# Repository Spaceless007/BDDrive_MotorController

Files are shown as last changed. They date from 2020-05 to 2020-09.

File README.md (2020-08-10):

# BDDrive_MotorController
Modifications done on the open source ODrive project to support one low current brushless DC motor

## Introduction
This project is based on a open source porjet named [ODrive](https://odriverobotics.com/). ODrive is a high power brushless DC motor controller. The main goal of the BDDrive is to modify the ODrive v3.4 to accomodate special needs for a tension controlled braided carrier of composites master's project. In short, there are two main reasons why the BDDrive was conceive. 

Firstly, the most recent ODrive someone can buy is the version v3.6, which was the board used first for testing if this board could be useful for the carrier. Almost everything about the ODrive is open source. The firmware is totally available for free [at this repository](https://github.com/madcowswe/ODrive). Most of the hardware is available, except for the most recent versions v3.5 and v3.6. The creator of the project started to see people copying the project and selling it at a lower price, so he decided to stop to make available the hardware design of the newer versions.Since the most recent board which is on the [hardware github repository](https://github.com/madcowswe/ODriveHardware) is the ODrive v3.4, and this board has many issues, well, it needed to be modified on the BDDrive.

Secondly, ODrive is a **high power** motor controller, it can control motors up to high current (something like 60 Amps, maybe even more). But the carrier is not using high power motors, the highest it goes is around 5 Amps. Since the ODrive is designed for higher current motors, it isn't the best for controlling motor like the tension controlled braided carrier is using. So we needed to fix this on the BDDrive. 

## Repository layout
Here is how the repository is organized and what folder contains what:
- Documentation: contains general documentation for the board
  - Ressources: contains various useful diagrams
  - Requirements: contains files where the requierements of the board are explained, what was modified and for what reason
  - Shunt test: contains screen shots of a test done using a ODrive v3.6 with new shunt resistors designed for low power DC brushless motors
- Hardware: contains the Altium Designer files for the BDDrive embedded circuit (electrical schematics)
  - CAD: contains .step files for electrical integrated circuits (IC) and also a .step file for the whole BDDrive board
  - BOM: contains the bill of materials for the board
  - gerbers: contains files generated with Altium Designer to produce the circuit with the JLC PCB or PCB Way company
  - Altium_libs: contains custom libraries for various electrical parts in the PCB (printed circuit board)
  - v3.4_nbd: contains the schematics and the PCB files for the BDDrive
  - v3: contains the schematics for the ODrive v3.4 board

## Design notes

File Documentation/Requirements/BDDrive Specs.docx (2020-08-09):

1. HARDWARE COMPARAISON

ODrive v3.4

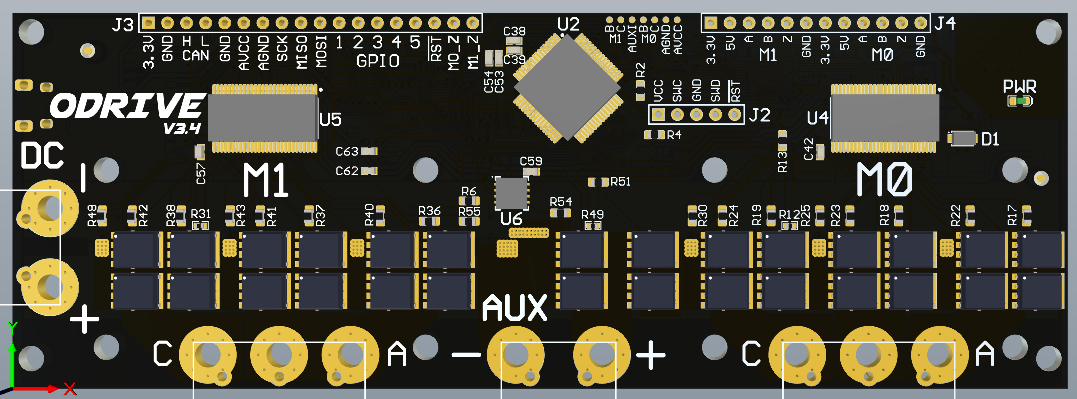
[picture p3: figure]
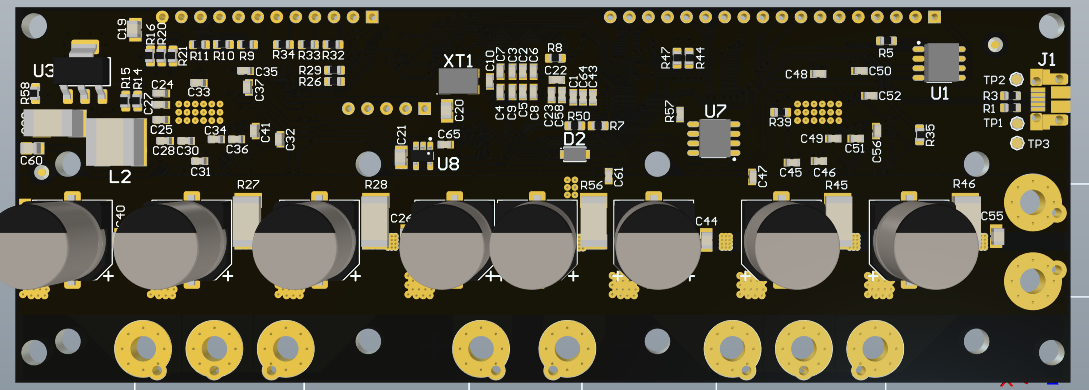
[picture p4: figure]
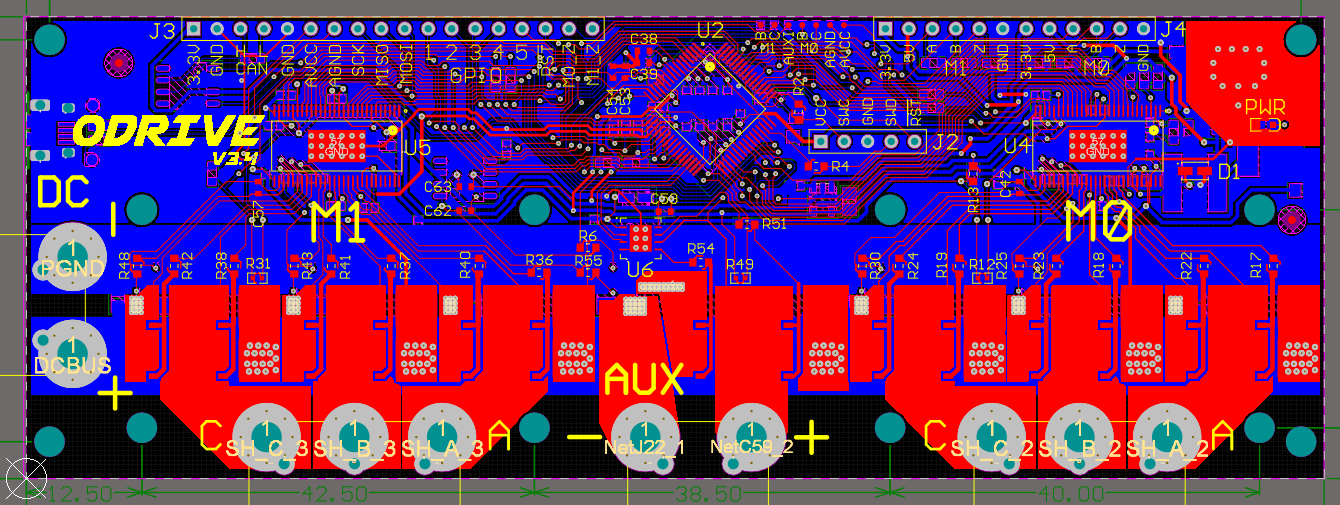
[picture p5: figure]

BDDrive : ODrive v3.4 modified

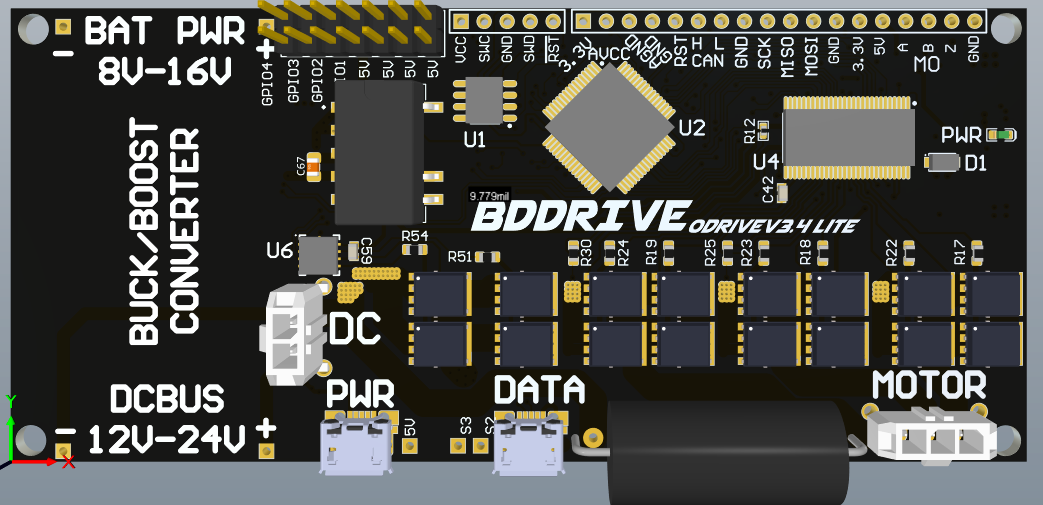
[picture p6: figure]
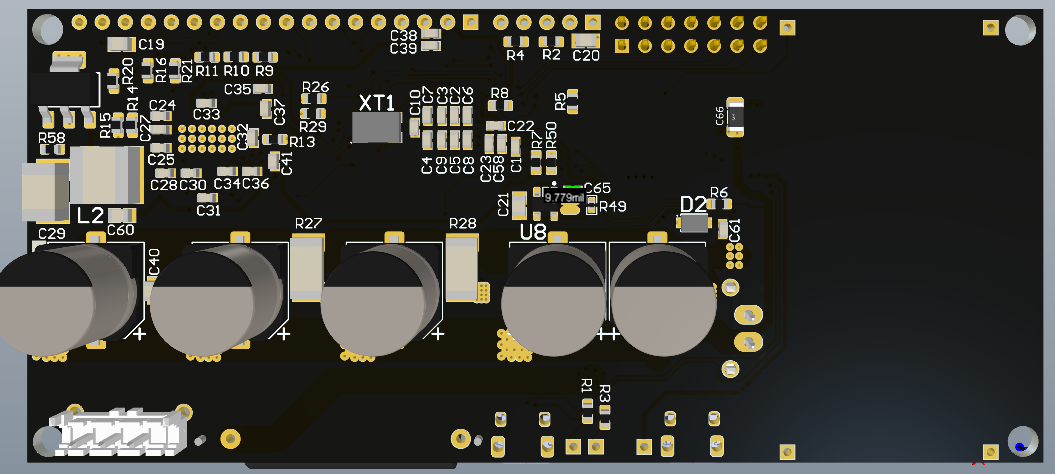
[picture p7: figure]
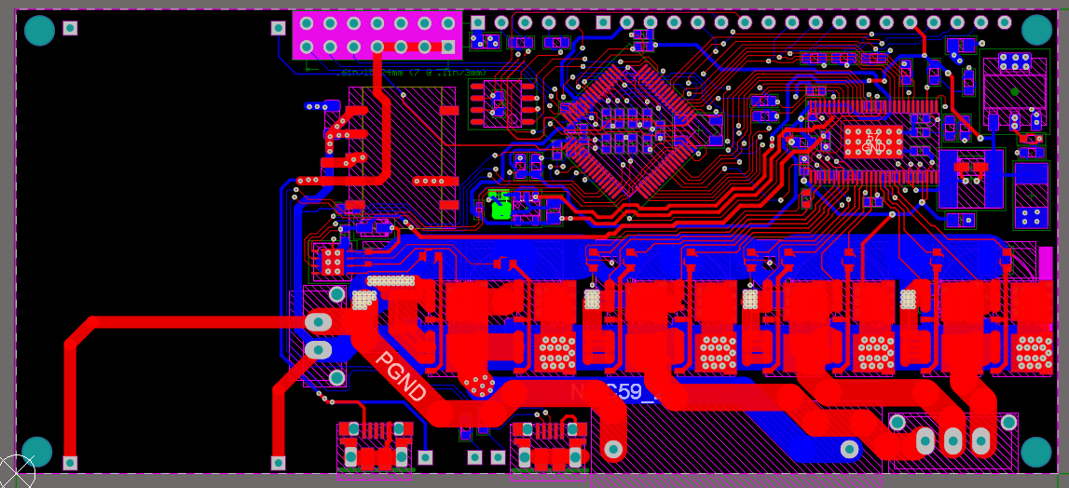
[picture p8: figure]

The polygon pours are not shown on this board, or else we wouldn`t see anything

2. MODIFICATIONS
- Remove support for two motors (remove M1), so right now BDDrive can only control one brushless DC motor
- Add support for a Buck/Boost converter breakout board soldered directly on the BDDrive
  - The breakout board needs to be within these specs: input from 8 to 16 volts and output configured as 12 to 24 volts
  - Don’t go over 24V (not even 24,5V), the BDDrive doesn’t support it
- Replace power resistor connector for a power resistor soldered directly on the board
  - Also, this resistor is rectangular (even though it is showed as round in the picture above) to be able to put mini heat sinks on it
- Use Molex connectors instead of screw in connectors to facilitate harness setup and the screw in connectors were proven as unreliable
- Add another 5V @ 1A power supply designed to power a Raspberry Pi with it (the power consumption of a Raspberry Pi Zero was estimated that the would be to be under 200 mA, so you can add 5V mini cooling fans with the 4 power pints available)
- Add external header with 5V supply outputs (4 power pins and 4 GND pins) and access to GPIO ports (3 GPIO pins and 3 GND pins)
- Add a power micro USB connector connected to the new 5V supply to power the Raspberry Pi
- Reroute a lot of components to minimize the size of the PCB
- Fix problems with the ODrive v3.4 which are documented here:
  - From the hardware GitHub: https://github.com/madcowswe/ODriveHardware
    - Check docs of v3.4 and v3.5 folders
    - Check CHANGELOG.md of v3 folder
  - https://discourse.odriverobotics.com/t/drv-fault-on-odrive-v3-4/558?u=madcowswe
  - Go from two layers to four layers to keep the GND uniformed
  - Fix routing problems
- Modify shunt resistors to be able to have a low power motor (below 5 Amps)
  - https://discourse.odriverobotics.com/t/current-sensing-resistor-for-low-current-motors/377/2
  - https://discourse.odriverobotics.com/t/maxon-272763-motor/989/8

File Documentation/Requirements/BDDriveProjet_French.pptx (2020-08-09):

## CONCEPTION D’UN CIRCUIT IMPRIMÉ POUR UN DÉBOBINEUR ASSERVI A FIL ROBOTISÉ POUR LE TRESSAGE NON-LINÉAIRE DES FIBRES COMPOSITES

NATHANAËL BEAUDOIN-DION
2020/05/07

## AGENDA

- Characterisation of single yarn microstructure

- Présentation du projet & des requis
- Ce qu’il a été fait
- Ce qu’il reste à faire
- Échéancier
- Budget

## PRÉSENTATION DU PROJET & DES REQUIS

NATHANAËL BEAUDOIN-DION
2020/05/07

## PRÉSENTATION DU PROJET

- Originalement, Cristian utilisait un circuit imprimé nommé ODrive v3.6 et il fonctionne bien
- Cependant, le PCB (Printed Circuit Board) est trop gros et il supporte deux moteurs, ce qui n’est pas necessaire
- Ainsi, je suis parti du schema électrique du ODrive v3.4 (v3.6 n’est pas disponible) pour ensuite le modifier
- Donc ce PCB doit controller un moteur et il doit communiquer avec un Raspberry Pi afin de pouvoir être controlé à distance (projet de Mathieu)

## PRÉSENTATION DU PROJET

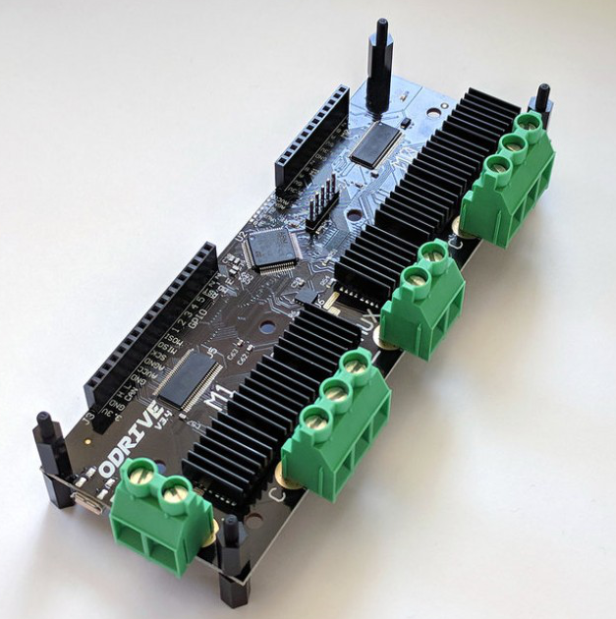
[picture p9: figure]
ODrive v3.6 24V on RoboRium in India Canada USA Bangladesh Nepal ...

ODrive v3.6

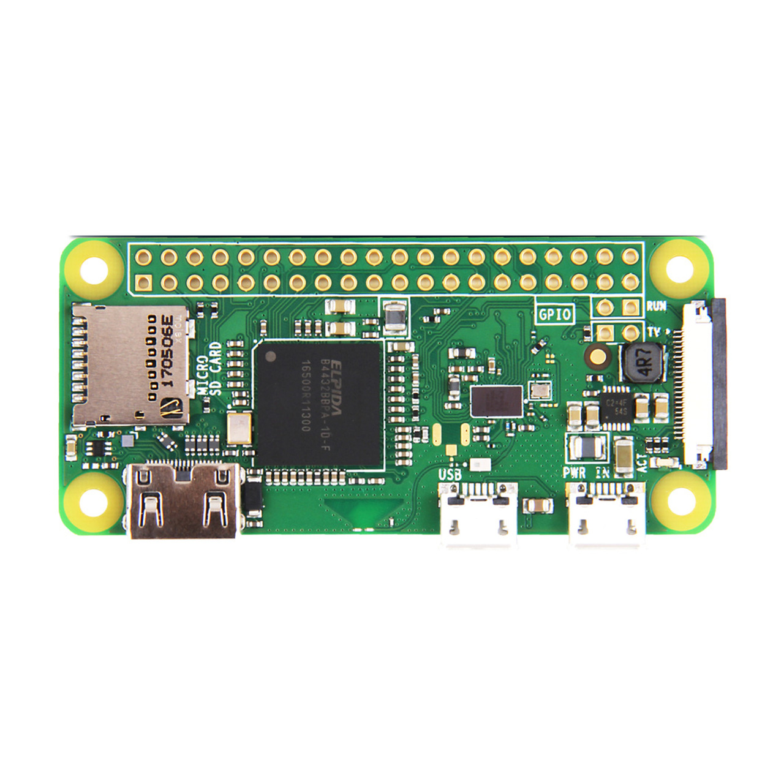
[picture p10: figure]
Raspberry Pi Zero W

Raspberry Pi Zero W

## PRÉSENTATION DES REQUIS

Le ODrive modifié, appelé BDDrive, doit :
- Contrôler un moteur de type “brushless” à l’aide d’un encodeur précisément
- Freiner le moteur avec une résistance de puissance intégrée au PCB
- Communiquer en sériel avec un connecteur microUSB
- Être alimenté par une batterie par différents voltages (12v, 15v, 20v, 24v) puis calibrer son alimentation à 12V
- Alimenté avec du 5V le Raspberry Pi avec un connecteur microUSB
- Avoir des pins “varia” pour par exemple alimenté des ventilateurs
- Être le plus petit possible

## CE QU’IL A ÉTÉ FAIT

NATHANAËL BEAUDOIN-DION
2020/05/07

## CE QU’IL A ÉTÉ FAIT

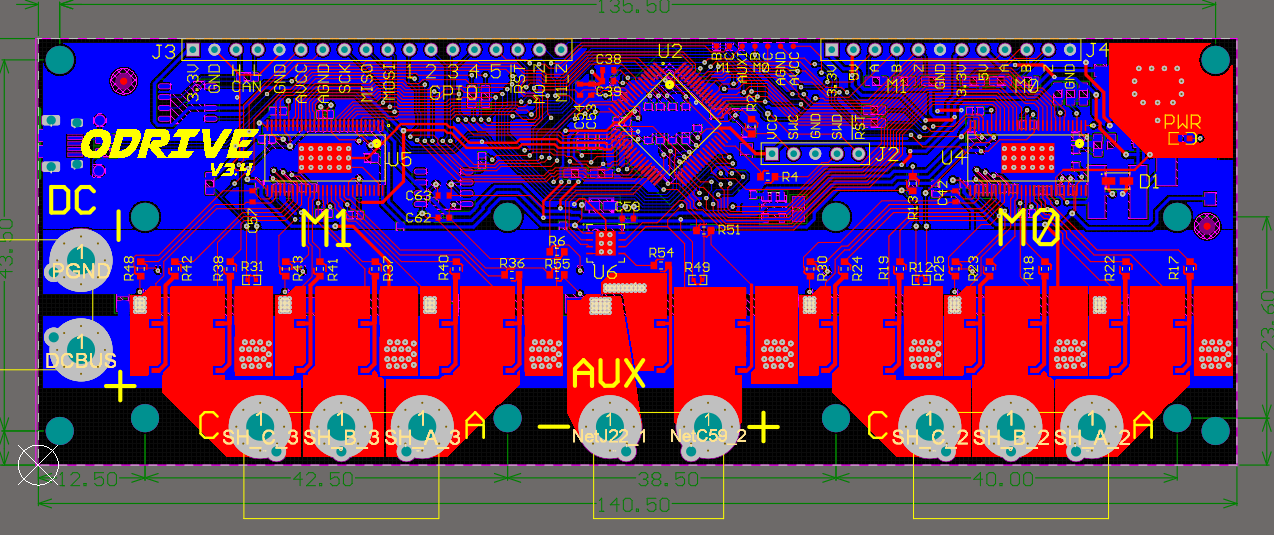
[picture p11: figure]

BDDrive

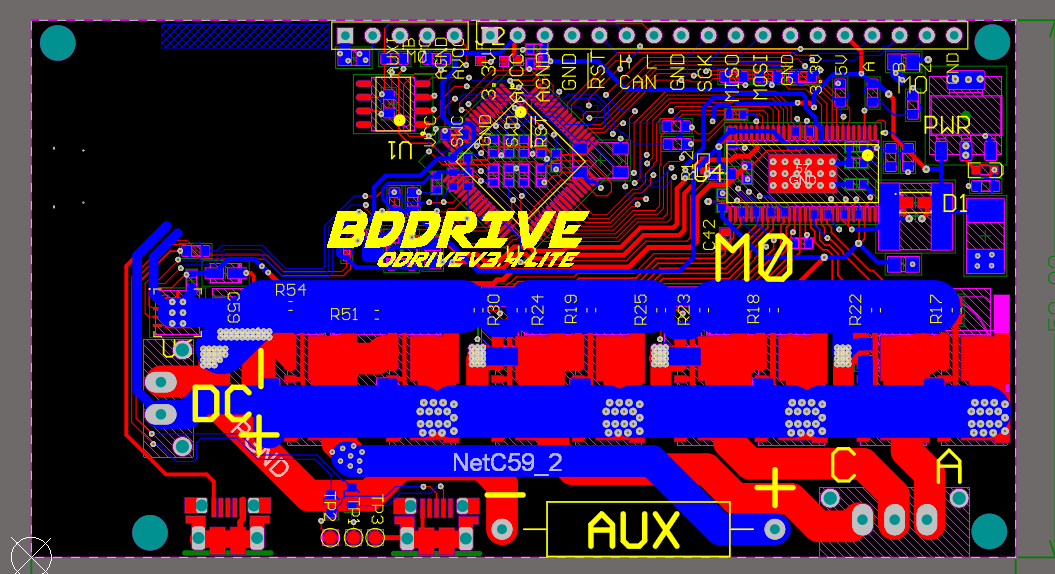
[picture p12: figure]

ODrive v3.4

## CE QU’IL A ÉTÉ FAIT

- Plusieurs tests sur le ODrive v3.6 et ODrive v3.4 ont été fait afin de vérifier leur fonctionnement
  - Pour v3.6 : changer des résistances pour diminuer le bruit
  - Pour v3.4 : vérifier qu’il fonctionne normalement
- Design à partir du ODrive v3.4 le BDDrive
  - Régler plusieurs problèmes présents dans le PCB au niveau logique et physique
  - Reroutage du PCB afin de diminuer sa taille le plus possible
  - Ajouter des nouvelles résistances
  - Modification des connecteurs (pour diminuer la taille du PCB)
  - Ajout d’un connecteur microUSB pour alimenté le Raspberry Pi

## CE QU’IL A ÉTÉ FAIT

- Recherche et compréhension générale du projet Open Source ODrive, comment le faire fonctionner, debug les problèmes du setup de programmation
  - 10h00
- Tests avec le ODrive 3.6 avec deux tests benchs différents (pré et post COVID)
  - 8h00
- Production et soudure du ODrive v3.4
  - 14h00
- Premiers tests sur le ODrive v3.4
  - 4h00
- Début du design du BDDrive, recherche sur internet de ses problèmes
  - 26h00

## CE QU’IL RESTE À FAIRE

NATHANAËL BEAUDOIN-DION
2020/05/07

## CE QU’IL RESTE À FAIRE

- Finir les tests sur ODrive v3.4 (5h00)
  - Tests software
- Finir le design du BDDrive (20h00)
  - Ajout du régulateur de tensión 5V 1A pour l’alimentation du Raspberry Pi
  - Ajout du circuit d’alimentation du BDDrive à partir d’une batterie, avec différents voltages afin de output un 12V constant
  - Ajout d’un connecteur varia
  - Ajout d’une lecture de tension de la batterie
- Production et soudure du BDDrive (12h00 de travail, mais beaucoup d’attente)
  - Peut potentiellement prendre beaucoup de temps à cause du COVID-19
- Tests du BDDrive (minimum 5h)

## ÉCHÉANCIER

NATHANAËL BEAUDOIN-DION
2020/05/07

## ÉCHÉANCIER DU MOIS DE MAI

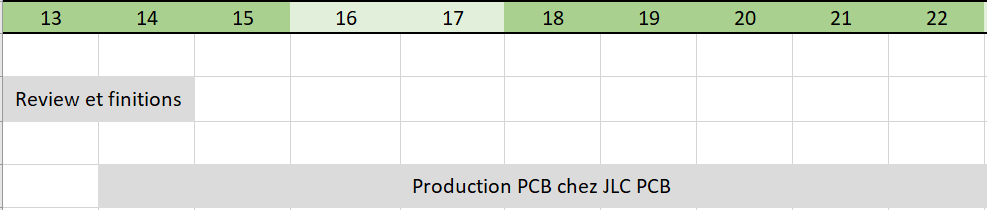
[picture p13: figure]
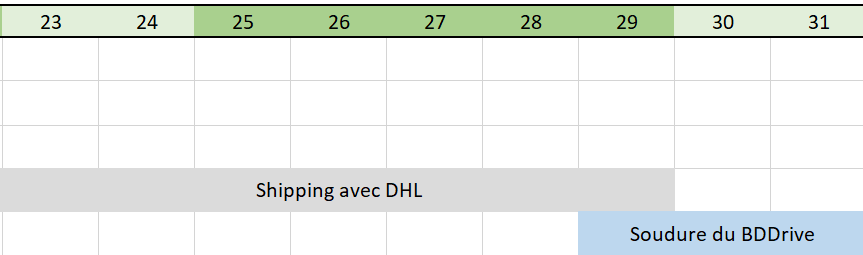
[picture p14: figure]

## BUDGET

NATHANAËL BEAUDOIN-DION
2020/05/07

## BUDGET

- Ce qu’il a déjà été dépensé :
  - Production et soudure du ODrive v3.4 : 229.25 CAD $ + 30.10 USD $
- Ce qu’il reste à dépensé pour la conception du BDDrive :
  - Production PCB à 5 exemplaires en 5 jours: 75 USD $ (+29 en 3 jours, +58 en 2 jours)
  - Production PCB à 100 exemplaires en 8 jours: 215 USD $
  - Pièces électroniques pour 1 exemplaire : environ 100 CAD $
  - Pièces électroniques pour 100 exemplaires : au dessus de 6,000 CAD $

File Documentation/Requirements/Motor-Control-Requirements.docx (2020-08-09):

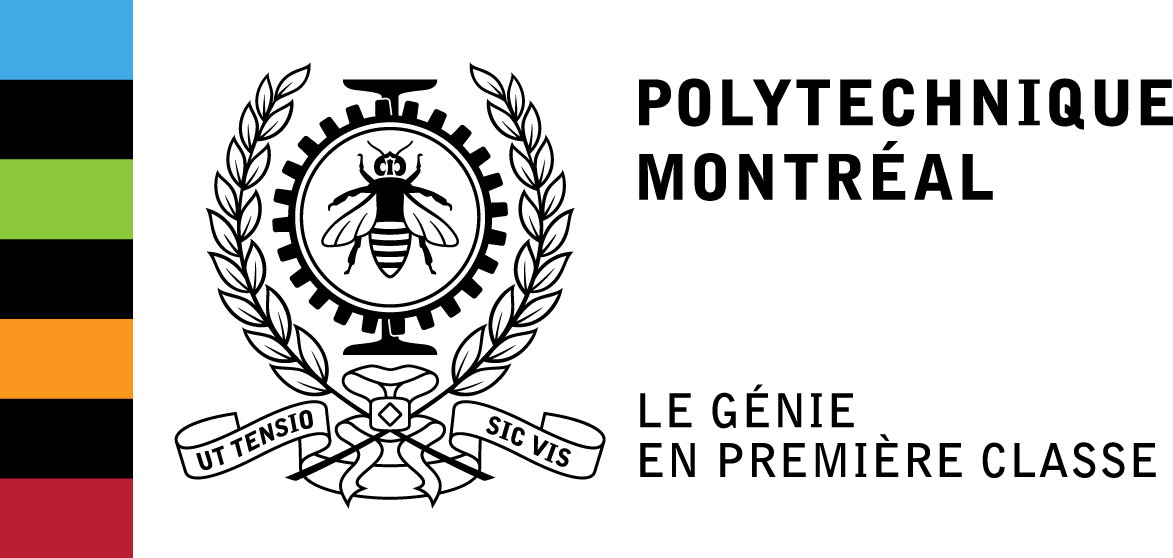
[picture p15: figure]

Masters Project – Design of a Torque-Controlled Carrier for Non-Linear Braiding of Composite Materials

TECHNICAL REQUIREMENTS FOR THE MOTOR CONTROL SYSTEM BASED ON THE ODRIVE ROBOTICS MODULE

presented to :

Louis Laberge Lebel

by :

Cristian Talos | 1794712 | ___________________________________________

2020/01/05
Montréal

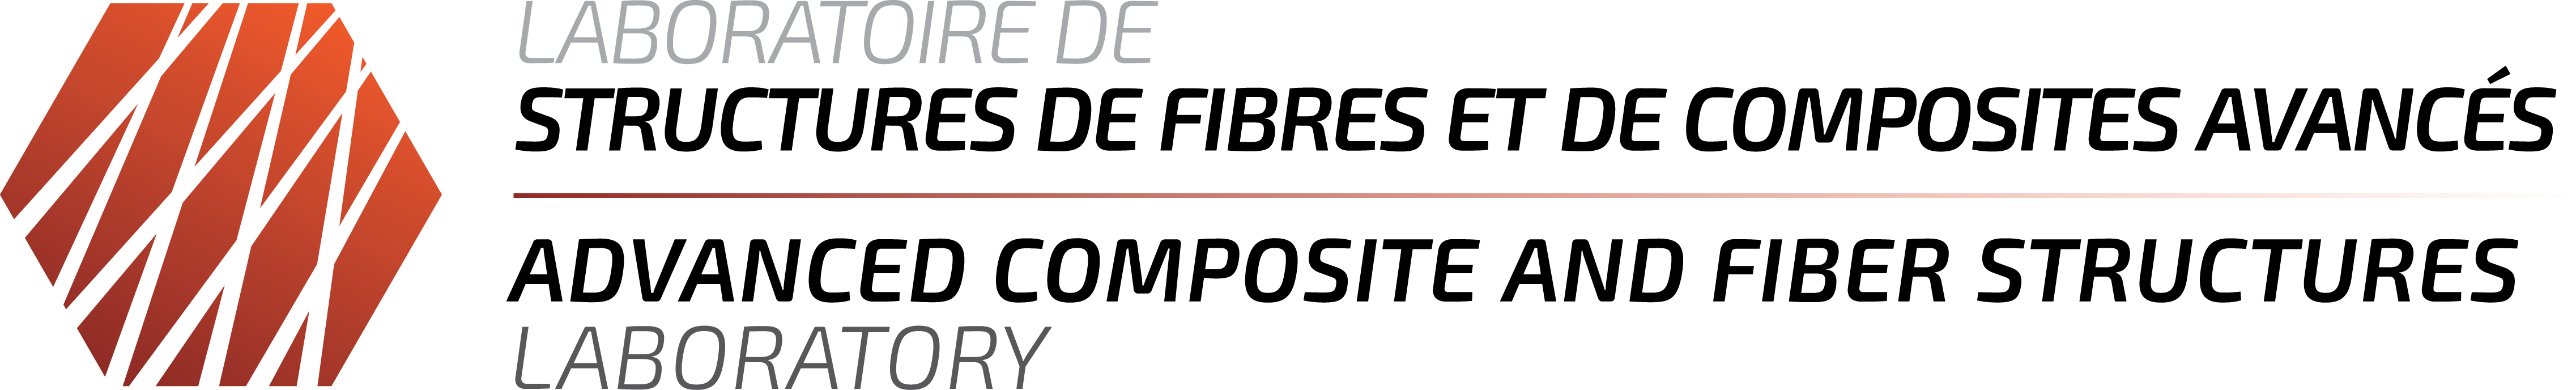
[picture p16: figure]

Table of Contents

# Introduction

Currently, a system is being designed to be used in the braiding of composite materials and other subjects related to spool un-winding at controlled torque. Multiple tests have been made using a hobby brushless motor and the ODrive module v3.6, 24v. The tests have been conclusive and now the the project has to move on to the next phase, in which the ODrive module have to be adapted to our application. This present report will detail the technical requirements of the newly designed board based on the open-sourced hardware and firmware of the ODrive v3.6.

# Project Overview

During the braiding process, the composite fiber (such as carbon, glass, aramid) has to be under a small tension (force) so that the fibers braid properly with good mechanical properties. Currently, the industrial braiding carriers uses springs, rollers and a release mechanism to ensure a certain force, but these mechanisms are not effective because the force is not constant due to the compression and decompression of the springs, and because at each release mechanism, there is an impact force on the fibers that damages prematurely the integrity of the material. To overcome these mechanical issues and to improve the mechanical performances, a torqued-controlled carrier will be used, thus replacing all mechanical components by a more compact and more efficient system. Although this solution will improve performances, it also has its challenges, such as carrying a battery for an 8h autonomy while being as compact and light as possible. The tests that has been made with the ODrive have been conclusive and it will be able to deliver the required performances after some modifications. For the braiding carrier, the range of force during the braiding is below 5N, which translates approximately to a current below 15A in the BLDC motor (in the d-q rotating reference plane), depending on the radius of the final spool design. In the following section, a brief overlook will be made on the currently used ODrive module, with specific remarks on critical components. The ODrive module is composed of both hardware and firmware.

# ODrive Module – Hardware and Firmware

The ODrive’s hardware is capable of running two BLDC motors (and two encoders), using a bus supply from 12 to 24vDC. Each of the motors is controlled by an DRV8301 driver that uses two shunt resistors (on phase B and C) to provide a feedback on the current of the motor. The current design of the ODrive uses shunt resistors that can handle currents over 60A, which is way beyond the scope of the braiding carrier. This translates in a current reading that has a lot of noise for low current applications, which causes performance issues. Regarding the firmware, it has to be modified to incorporate all the changes brought to the board (such as modyfing the shunt resistors values).

# New Requirements

In the scope of the masters project, it has been determined that the fastest way to proceed is to change as little as possible the ODrive v3.6 module until a first prototype has been made as a proof of concept for the torque-controlled braiding carrier. After the proof of concept has been made, a completely new electronics board will be designed to minimize the volume of the electronics, making the prototype more compact. Here is a list of requirements:

1. Control one single BLDC motor and one single encoder
2. Use shunt resistors to handle up to 15A
3. Reduce the size of the board as much as possible
4. Compatibility with the Battery Management System (BMS) for a 4 cell Lithium-Polymer battery (14.8v)
5. Compatibility with a Raspberry Pi Zero Wireless

TECHNICAL REQUIREMENTS FOR THE MOTOR CONTROL SYSTEM BASED ON THE ODRIVE ROBOTICS MODULE Page: 1 de 4 Date: 2020/01/05

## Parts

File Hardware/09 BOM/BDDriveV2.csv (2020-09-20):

Quantity | Designator | Description | Comment | LibRef
2 | C1, C27 | CAP CER 270PF 50V NP0 0603 | 270pF | GRM1885C1H271JA01D
2 | C2, C3 | CAP CER 10PF 50V NP0 0603 | 10pF | GRM1885C1H100JA01D
9 | C4, C5, C23, C32, C35, C37, C58, C61, C65 | CAP CER 2.2UF 16V X5R 0603 | 2.2µF | GRM188R61C225KE15D
13 | C6, C7, C8, C9, C10, C22, C25, C28, C30, C31, C34, C41, C59 | CAP CER 0.1UF 25V X7R 0603 | 0.10µF | GRM188R71E104KA01D
5 | C11, C12, C13, C14, C15 | CAP, FP Series, 470 µF, 25 V, Radial Can - SMD, 10 mm | 470uF | EEEFP1E471AP
5 | C19, C20, C21, C40, C60 | CAP CER 4.7UF 35V X5R 0805 | 4.7uF | GRM219R6YA475KA73D
1 | C24 | CAP CER 82PF 100V NP0 0603 | 82pF | GRM1885C2A820JA01D
1 | C29 | CAP TANT 68UF 16V 20% 2312 250mOhm | 68uF | T495C686M016ATE250
3 | C33, C100, C101 | CAP CER 0.022UF 25V X7R 0603 | 0.022µF | GRM188R71E223KA01D
4 | C36, C38, C39, C42 | CAP CER 2200PF 50V NP0 0603 | 2200pF | GRM1885C1H222JA01D
1 | C66 | CAP CER 10UF 50V X5R 1206 | 10µF | CL31A106KBHNNNE
1 | C67 | CAP CER 22UF 25V X5R 0805 | 22µF | GRM21BR61E226ME44L
2 | D1, D2 | Rectifier Diode, Single, 40 V, 1 A, SOD-123FL, 2, 550 mV |  | MBR140SFT1G
4 | H1, H2, H3, H4 | M3 Hole with no copper |  | M3 Hole
2 | J1, J30 | MICRO USB B, RECEPTACLE, SMT, RA, 5WAY |  | 10103594-0001LF
1 | J2 | Header, 5-Pin |  | Header 5
1 | J3 | Header, 18-Pin | Header 18 | Header 18
1 | J9 | CONN HEADER 2POS VERT TIN T/H | 0436500227 | 0436500227
1 | J14 | CONN HEADER 3POS VERT TIN T/H | 0436500327 | 0436500327
1 | J100 | No Description Available | Part Number: 67996-114HLF | 67996-114HLF
1 | L2 | INDUCTOR 22UH 1.4A 175.5 MOHM | 22uH | NR6028T220M
1 | LED1 | LED GREEN CLEAR 0603 SMD | Green | LTST-C190KGKT
1 | PS1 |  | V78E05-1000-SMT-TR | V78E05-1000-SMT-TR
16 | Q1, Q2, Q3, Q4, Q5, Q6, Q7, Q8, Q9, Q10, Q11, Q12, Q25, Q26, Q27, Q28 | MOSFET N-CH 30V 13A SO8FL | NTMFS4935NT1G | NTMFS4935NT1G
6 | R1, R2, R3, R4, R26, R29 | RES SMD 22 OHM 1% 1/10W 0603 | 22R | RC0603FR-0722RL
3 | R5, R25, R30 | RES SMD 120 OHM 1% 1/10W 0603 | 120R | RC0603FR-07120RL
1 | R6 | RES SMD 10K OHM 1% 1/10W 0603 | 10K | RC0603FR-0710KL
2 | R7, R58 | RES SMD 1K OHM 1% 1/10W 0603 | 1k | RC0603FR-071KL
2 | R8, R14 | RES SMD 47K OHM 1% 1/10W 0603 | 47K | RC0603FR-0747KL
6 | R9, R10, R11, R13, R20, R50 | RES SMD 3.3K OHM 1% 1/10W 0603 | 3.3k | RC0603FR-073K3L
2 | R12, R49 | THERMISTOR 10K OHM NTC 0402 SMD | NCP15XH103F03RC | NCP15XH103F03RC
1 | R15 | RES SMD 220K OHM 1% 1/10W 0603 | 220k | RC0603FR-07220KL
2 | R16, R21 | RES SMD 18K OHM 1% 1/10W 0603 | 18k | RC0603FR-0718KL
8 | R17, R18, R19, R22, R23, R24, R51, R54 | RES SMD 2.2 OHM 1% 1/10W 0603 | 2.2R | RC0603FR-072R2L
2 | R27, R28 | RES SMD 0.015OHM 1% 3W 2512 | CSR2512C0R015F | CSR2512C0R015F
1 | R100 | RES SMD 100K OHM 1% 1/10W 0603 | 100k | ERJ-3EKF1003V
1 | R101 | RES SMD 12K OHM 1% 1/10W 0603 | 12k | ERJ-3EKF1202V
1 | R103 | RES 1 OHM 5W 5% AXIAL | 1 | SQP500JB-1R0
1 | R104 | RES 10.2K OHM 0.1% 1/8W 0805 | 10.2K | ERA-6AEB1022V
1 | R105 | RES 42.2K OHM 0.1% 1/8W 0805 | 42.2k | ERA-6AEB4222V
1 | U1 | 3.3-V CAN Bus Transceiver |  | SN65HVD232D
1 | U2 | ARM Cortex-M4 32-bit MCU+FPU, 210 DMIPS, 1024 kB Flash, 192 kB Internal RAM, 51 I/Os, 64-pin LQFP, -40 to 85 degC, Tray |  | STM32F405RGT6
1 | U3 | IC REG LDO 3.3V 1A SOT223 | 3.3V | AZ1117EH-3.3TRG1
1 | U4 | MOTOR DRIVER, 3PH, 56HTSSOP |  | DRV8301
1 | U6 | DRIVER, MOSFET, HALF BRIDGE, WSON-8, 1A |  | LM5109BSD/NOPB
1 | U8 | IC REG LDO 3.3V 0.25A SOT23-5 | 3.3V | LP5907MFX-3.3/NOPB
1 | XT1 | Crystal 8MHz ±10ppm 10pF 200 Ohm -10°C ~ 60°C Surface Mount 4-SMD, No Lead (DFN, LCC) | ABM3B-8.000MHZ-10-1-U-T | ABM3B-8.000MHZ-10-1-U-T

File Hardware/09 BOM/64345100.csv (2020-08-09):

# | QUANTITY | PART NUMBER | MANUFACTURER PART NUMBER | DESCRIPTION | CUSTOMER REFERENCE | BACKORDER | UNIT PRICE | EXTENDED PRICE
1 | 10 | 490-1437-1-ND | GRM1885C1H271JA01D | CAP CER 270PF 50V C0G/NP0 0603 |  | 0 | 0.16600 Discount | 1.66
2 | 10 | 490-1403-1-ND | GRM1885C1H100JA01D | CAP CER 10PF 50V C0G/NP0 0603 |  | 0 | 0.11800 Discount | 1.18
3 | 15 | 399-7886-1-ND | C0603C225K4PACTU | CAP CER 2.2UF 16V X5R 0603 |  | 0 | 0.14000 Discount | 2.10
4 | 20 | 399-1283-1-ND | C0603C104M3RACTU | CAP CER 0.1UF 25V X7R 0603 |  | 0 | 0.08100 Discount | 1.62
5 | 10 | PCE3909CT-ND | EEE-1EA471P | CAP ALUM 470UF 20% 25V SMD |  | 0 | 0.62500 Discount | 6.25
6 | 10 | 490-7208-1-ND | GRM219R6YA475KA73D | CAP CER 4.7UF 35V X5R 0805 |  | 0 | 0.28800 Discount | 2.88
7 | 5 | 490-1349-1-ND | GRM1885C2A820JA01D | CAP CER 82PF 100V C0G/NP0 0603 |  | 0 | 0.17000 Discount | 0.85
8 | 2 | 399-10452-1-ND | T495C686M016ATE250 | CAP TANT 68UF 20% 16V 2312 |  | 0 | 1.34000 Discount | 2.68
9 | 5 | 399-9043-1-ND | C0603C223J3RACTU | CAP CER 0.022UF 25V X7R 0603 |  | 0 | 0.15000 Discount | 0.75
10 | 10 | 490-1459-1-ND | GRM1885C1H222JA01D | CAP CER 2200PF 50V C0G/NP0 0603 |  | 0 | 0.13400 Discount | 1.34
11 | 2 | 1276-2876-1-ND | CL31A106KBHNNNE | CAP CER 10UF 50V X5R 1206 |  | 0 | 0.81000 Discount | 1.62
12 | 3 | 490-10749-1-ND | GRM21BR61E226ME44L | CAP CER 22UF 25V X5R 0805 |  | 0 | 0.74000 Discount | 2.22
13 | 5 | MBR140SFT1GOSCT-ND | MBR140SFT1G | DIODE SCHOTTKY 40V 1A SOD123L |  | 0 | 0.54000 Discount | 2.70
14 | 3 | H125272CT-ND | ZX62D-B-5P8(30) | CONN RCPT USB2.0 MICRO B SMD R/A |  | 0 | 1.36000 Discount | 4.08
15 | 2 | S7016-ND | PPTC181LFBN-RC | CONN HDR 18POS 0.1 TIN PCB |  | 0 | 1.49000 Discount | 2.98
16 | 2 | S6103-ND | PPTC051LFBN-RC | CONN HDR 5POS 0.1 TIN PCB |  | 0 | 0.65000 Discount | 1.30
17 | 2 | WM10656-ND | 0436500227 | CONN HEADER VERT 2POS 3MM |  | 0 | 1.09000 Discount | 2.18
18 | 2 | WM7500-ND | 0436500327 | CONN HEADER VERT 3POS 3MM |  | 0 | 1.36000 Discount | 2.72
19 | 2 | 609-3491-ND | 67996-114HLF | CONN HEADER VERT 14POS 2.54MM |  | 0 | 1.04000 Discount | 2.08
20 | 2 | 587-2103-1-ND | NR6028T220M | FIXED IND 22UH 1.4A 175.5 MOHM |  | 0 | 0.53000 Discount | 1.06
21 | 2 | 102-5033-1-ND | V78E05-1000-SMT-TR | DC-DC NON-ISOLATED, 1 A, 8 36 VD |  | 0 | 6.84000 Discount | 13.68
22 | 15 | NTMFS4935NT1GOSCT-ND | NTMFS4935NT1G | MOSFET N-CH 30V 13A SO8FL |  | 0 | 1.04400 Discount | 15.66
23 | 10 | 311-22.0HRCT-ND | RC0603FR-0722RL | RES SMD 22 OHM 1% 1/10W 0603 |  | 0 | 0.03400 | 0.34
24 | 10 | 311-120HRCT-ND | RC0603FR-07120RL | RES SMD 120 OHM 1% 1/10W 0603 |  | 0 | 0.03400 | 0.34
25 | 10 | 311-1.00KHRCT-ND | RC0603FR-071KL | RES SMD 1K OHM 1% 1/10W 0603 |  | 0 | 0.03400 | 0.34
26 | 10 | 311-47.0KHRCT-ND | RC0603FR-0747KL | RES SMD 47K OHM 1% 1/10W 0603 |  | 0 | 0.03400 | 0.34
27 | 10 | 311-3.30KHRCT-ND | RC0603FR-073K3L | RES SMD 3.3K OHM 1% 1/10W 0603 |  | 0 | 0.03400 | 0.34
28 | 5 | 490-4801-1-ND | NCP15XH103F03RC | THERMISTOR NTC 10KOHM 3380K 0402 |  | 0 | 0.19000 Discount | 0.95
29 | 10 | 311-220KHRCT-ND | RC0603FR-07220KL | RES SMD 220K OHM 1% 1/10W 0603 |  | 0 | 0.03400 | 0.34
30 | 10 | 541-10.0KHCT-ND | CRCW060310K0FKEA | RES SMD 10K OHM 1% 1/10W 0603 |  | 0 | 0.05500 | 0.55
31 | 10 | 541-18.0KHCT-ND | CRCW060318K0FKEA | RES SMD 18K OHM 1% 1/10W 0603 |  | 0 | 0.05500 | 0.55
32 | 10 | 311-2.2HRCT-ND | RC0603FR-072R2L | RES SMD 2.2 OHM 1% 1/10W 0603 |  | 0 | 0.06700 Discount | 0.67
33 | 3 | 696-1673-1-ND | CSR2512C0R015F | RES 0.015 OHM 1% 3W 2512 |  | 0 | 0.93000 Discount | 2.79
34 | 2 | 1.0W-5-ND | SQP500JB-1R0 | RES 1 OHM 5W 5% AXIAL |  | 0 | 0.88000 Discount | 1.76
35 | 1 | 296-12282-5-ND | SN65HVD232D | IC TRANSCEIVER HALF 1/1 8SOIC |  | 0 | 3.39000 Discount | 3.39
36 | 1 | 497-11767-ND | STM32F405RGT6 | IC MCU 32BIT 1MB FLASH 64LQFP |  | 0 | 16.79000 Discount | 16.79
37 | 2 | AZ1117EH-3.3TRG1DICT-ND | AZ1117EH-3.3TRG1 | IC REG LINEAR 3.3V 1A SOT223 |  | 0 | 0.61000 Discount | 1.22
38 | 1 | 296-29433-1-ND | DRV8301DCAR | IC MOTOR DRIVER 6V-60V 56HTSSOP |  | 0 | 8.44000 Discount | 8.44
39 | 1 | LM5109BSD/NOPBCT-ND | LM5109BSD/NOPB | IC GATE DRVR HALF-BRIDGE 8WSON |  | 0 | 1.25000 Discount | 1.25
40 | 2 | 296-38557-1-ND | LP5907MFX-3.3/NOPB | IC REG LINEAR 3.3V 250MA SOT23-5 |  | 0 | 0.79000 Discount | 1.58

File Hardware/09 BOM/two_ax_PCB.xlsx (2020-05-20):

Description | Designator
CAP CER 2.2UF 16V X5R 0603 | C1, C4, C5, C23, C32, C35, C37, C43, C47, C50, C52, C58, C61, C65
CAP CER 10PF 50V NP0 0603 | C2, C3 | need to buy
CAP CER 0.1UF 25V X7R 0603 | C6, C7, C8, C9, C10, C22, C25, C28, C30, C31, C34, C41, C45, C46, C49, C56, C59, C63
CAP, FP Series, 470 µF, 25 V, Radial Can - SMD, 10 mm | C11, C12, C13, C14, C15, C16, C17, C18
CAP CER 4.7UF 35V X5R 0805 | C19, C20, C21, C26, C40, C44, C55, C60
CAP CER 82PF 100V NP0 0603 | C24
CAP CER 270PF 50V NP0 0603 | C27
CAP TANT 68UF 16V 20% 2312 250mOhm | C29
CAP CER 0.022UF 25V X7R 0603 | C33, C48
CAP CER 2200PF 50V NP0 0603 | C36, C38, C39, C42, C51, C53, C54, C57, C62, C64
Rectifier Diode, Single, 40 V, 1 A, SOD-123FL, 2, 550 mV | D1, D2
INDUCTOR 22UH 1.4A 175.5 MOHM | L2
LED GREEN CLEAR 0603 SMD | LED1
MOSFET N-CH 30V 13A SO8FL | Q1, Q2, Q3, Q4, Q5, Q6, Q7, Q8, Q9, Q10, Q11, Q12, Q13, Q14, Q15, Q16, Q17, Q18, Q19, Q20, Q21, Q22, Q23, Q24, Q25, Q26, Q27, Q28
RES SMD 22 OHM 1% 1/10W 0603 | R1, R2, R3, R4, R26, R29, R44, R47
RES SMD 120 OHM 1% 1/10W 0603 | R5, R25, R30, R43, R48, R55, R57
RES SMD 10K OHM 1% 1/10W 0603 | R6
RES SMD 1K OHM 1% 1/10W 0603 | R7, R58
RES SMD 47K OHM 1% 1/10W 0603 | R8, R14
RES SMD 3.3K OHM 1% 1/10W 0603 | R9, R10, R11, R13, R20, R32, R33, R34, R35, R50
THERMISTOR 10K OHM NTC 0402 SMD | R12, R31, R49
RES SMD 220K OHM 1% 1/10W 0603 | R15
RES SMD 18K OHM 1% 1/10W 0603 | R16, R21, R39
RES SMD 2.2 OHM 1% 1/10W 0603 | R17, R18, R19, R22, R23, R24, R36, R37, R38, R40, R41, R42, R51, R54
RES SMD 0.0005 OHM 1% 3W 2512 | R27, R28, R45, R46, R56
3.3-V CAN Bus Transceiver | U1
ARM Cortex-M4 32-bit MCU+FPU, 210 DMIPS, 1024 kB Flash, 192 kB Internal RAM, 51 I/Os, 64-pin LQFP, -40 to 85 degC, Tray | U2
IC REG LDO 3.3V 1A SOT223 | U3
MOTOR DRIVER, 3PH, 56HTSSOP | U4, U5
DRIVER, MOSFET, HALF BRIDGE, WSON-8, 1A | 2
ANALOG DEVICES Current Sense Amplifier, Bidirectional, 1, 130 µA, NSOIC | U7
IC REG LDO 3.3V 0.25A SOT23-5 | U8
Crystal 8MHz ±10ppm 10pF 200 Ohm -10°C ~ 60°C Surface Mount 4-SMD, No Lead (DFN, LCC) | XT1

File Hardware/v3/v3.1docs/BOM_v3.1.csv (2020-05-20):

Quantity | Designator | Description | Comment | LibRef
14 | C1, C4, C5, C23, C32, C35, C37, C43, C47, C50, C52, C58, C60, C61 | CAP CER 2.2UF 16V X5R 0603 | 2.2µF | GRM188R61C225KE15D
2 | C2, C3 | CAP CER 10PF 50V NP0 0603 | 10pF | GRM1885C1H100JA01D
18 | C6, C7, C8, C9, C10, C22, C25, C28, C30, C31, C34, C41, C45, C46, C49, C56, C59, C63 | CAP CER 0.1UF 25V X7R 0603 | 0.10µF | GRM188R71E104KA01D
8 | C11, C12, C13, C14, C15, C16, C17, C18 | CAP, FP Series, 470 µF, 25 V, Radial Can - SMD, 10 mm | 470uF | EEEFP1E471AP
7 | C19, C20, C21, C26, C40, C44, C55 | CAP CER 4.7UF 35V X5R 0805 | 4.7uF | GRM219R6YA475KA73D
1 | C24 | CAP CER 82PF 100V NP0 0603 | 82pF | GRM1885C2A820JA01D
1 | C27 | CAP CER 270PF 50V NP0 0603 | 270pF | GRM1885C1H271JA01D
1 | C29 | CAP TANT 68UF 16V 20% 2312 250mOhm | 68uF | T495C686M016ATE250
11 | C33, C36, C38, C39, C42, C48, C51, C53, C54, C57, C62 | CAP CER 0.022UF 25V X7R 0603 | 0.022µF | GRM188R71E223KA01D
2 | D1, D2 | Rectifier Diode, Single, 40 V, 1 A, SOD-123FL, 2, 550 mV |  | MBR140SFT1G
12 | H1, H2, H3, H4, H5, H6, H7, H8, H9, H10, H11, H12 | M3 Hole with no copper |  | M3 Hole
1 | J1 | MICRO USB B, RECEPTACLE, SMT, RA, 5WAY |  | 10103594-0001LF
3 | J2, J10, J15 | Header, 5-Pin |  | Header 5
1 | J3 | Header, 3-Pin |  | Header 3
1 | J4 | Header, 4-Pin |  | Header 4
1 | J5 | Header, 3-Pin, Dual row |  | Header 3X2
1 | J6 | Header, 8-Pin |  | Header 8
10 | J7, J8, J11, J12, J13, J16, J17, J18, J21, J22 | M3 Spade Terminal |  | M3 Spade Terminal
2 | J9, J23 | MULTICOMP Wire-To-Board Terminal Block, 2, 600 V, 30 A, 24 AWG, 10 AWG |  | MC000054
2 | J14, J19 | TERMINAL BLOCK, WIRE TO BRD, 3POS, 10AWG |  | MC000051
1 | J20 | Socket | AuxV | Socket
1 | L1 | FERRITE BEAD, 0.1OHM, 2A, 0805 | 600ohm | 2508056017Y2
1 | L2 | INDUCTOR 22UH 1.4A 175.5 MOHM | 22uH | NR6028T220M
28 | Q1, Q2, Q3, Q4, Q5, Q6, Q7, Q8, Q9, Q10, Q11, Q12, Q13, Q14, Q15, Q16, Q17, Q18, Q19, Q20, Q21, Q22, Q23, Q24, Q25, Q26, Q27, Q28 | MOSFET, N CH, 30V, 70A, SO-8 FL |  | NTMFS4937NT1G
13 | R1, R2, R3, R4, R25, R26, R29, R30, R43, R44, R47, R48, R55 | RES SMD 22 OHM 1% 1/10W 0603 | 22R | RC0603FR-0722RL
1 | R5 | RES SMD 120 OHM 1% 1/10W 0603 | 120R | RC0603FR-07120RL
2 | R6, R52 | RES SMD 10K OHM 1% 1/10W 0603 | 10K | RC0603FR-0710KL
8 | R7, R9, R10, R11, R32, R33, R34, R53 | RES SMD 1K OHM 1% 1/10W 0603 | 1k | RC0603FR-071KL
2 | R8, R14 | RES SMD 47K OHM 1% 1/10W 0603 | 47K | RC0603FR-0747KL
3 | R12, R31, R49 | THERMISTOR 10K OHM NTC 0402 SMD | 10k | NCP15XH103F03RC
4 | R13, R20, R35, R50 | RES SMD 3.3K OHM 1% 1/10W 0603 | 3.3k | RC0603FR-073K3L
1 | R15 | RES SMD 220K OHM 1% 1/10W 0603 | 220k | RC0603FR-07220KL
3 | R16, R21, R39 | RES SMD 18K OHM 1% 1/10W 0603 | 18k | RC0603FR-0718KL
14 | R17, R18, R19, R22, R23, R24, R36, R37, R38, R40, R41, R42, R51, R54 | RES SMD 2.2 OHM 1% 1/10W 0603 | 2.2R | RC0603FR-072R2L
5 | R27, R28, R45, R46, R56 | RES SMD 0.0005 OHM 1% 3W 2512 | 500uOhm | CSR2512C0R0005F
1 | U1 | 3.3-V CAN Bus Transceiver |  | SN65HVD232D
1 | U2 | ARM Cortex-M4 32-bit MCU+FPU, 210 DMIPS, 1024 kB Flash, 192 kB Internal RAM, 51 I/Os, 64-pin LQFP, -40 to 85 degC, Tray |  | STM32F405RGT6
1 | U3 | IC, LDO, REG, 3.3V, SOT223 | 3.3V | AP1117E33G-13
2 | U4, U5 | MOTOR DRIVER, 3PH, 56HTSSOP |  | DRV8301
1 | U6 | DRIVER, MOSFET, HALF BRIDGE, WSON-8, 1A |  | LM5109BSD/NOPB
1 | U7 | ANALOG DEVICES Current Sense Amplifier, Bidirectional, 1, 130 µA, NSOIC |  | AD8418WBRZ
1 | XT1 | Crystal 8MHz ±10ppm 10pF 200 Ohm -10°C ~ 60°C Surface Mount 4-SMD, No Lead (DFN, LCC) | 8 MHz | ABM3B-8.000MHZ-10-1-U-T

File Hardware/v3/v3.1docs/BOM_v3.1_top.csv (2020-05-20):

Quantity | Designator | Description | Comment | LibRef | Layer
1 | C29 | CAP TANT 68UF 16V 20% 2312 250mOhm | 68uF | T495C686M016ATE250 | Top
7 | C38, C39, C42, C53, C54, C57, C62 | CAP CER 0.022UF 25V X7R 0603 | 0.022µF | GRM188R71E223KA01D | Top
2 | C59, C63 | CAP CER 0.1UF 25V X7R 0603 | 0.10µF | GRM188R71E104KA01D | Top
12 | H1, H2, H3, H4, H5, H6, H7, H8, H9, H10, H11, H12 | M3 Hole with no copper |  | M3 Hole | Top
3 | J2, J10, J15 | Header, 5-Pin |  | Header 5 | Top
1 | J3 | Header, 3-Pin |  | Header 3 | Top
1 | J4 | Header, 4-Pin |  | Header 4 | Top
1 | J5 | Header, 3-Pin, Dual row |  | Header 3X2 | Top
1 | J6 | Header, 8-Pin |  | Header 8 | Top
10 | J7, J8, J11, J12, J13, J16, J17, J18, J21, J22 | M3 Spade Terminal |  | M3 Spade Terminal | Top
2 | J9, J23 | MULTICOMP Wire-To-Board Terminal Block, 2, 600 V, 30 A, 24 AWG, 10 AWG |  | MC000054 | Top
2 | J14, J19 | TERMINAL BLOCK, WIRE TO BRD, 3POS, 10AWG |  | MC000051 | Top
1 | J20 | Socket | AuxV | Socket | Top
28 | Q1, Q2, Q3, Q4, Q5, Q6, Q7, Q8, Q9, Q10, Q11, Q12, Q13, Q14, Q15, Q16, Q17, Q18, Q19, Q20, Q21, Q22, Q23, Q24, Q25, Q26, Q27, Q28 | MOSFET, N CH, 30V, 70A, SO-8 FL |  | NTMFS4937NT1G | Top
7 | R2, R4, R25, R30, R43, R48, R55 | RES SMD 22 OHM 1% 1/10W 0603 | 22R | RC0603FR-0722RL | Top
1 | R5 | RES SMD 120 OHM 1% 1/10W 0603 | 120R | RC0603FR-07120RL | Top
2 | R6, R52 | RES SMD 10K OHM 1% 1/10W 0603 | 10K | RC0603FR-0710KL | Top
3 | R12, R31, R49 | THERMISTOR 10K OHM NTC 0402 SMD | 10k | NCP15XH103F03RC | Top
1 | R13 | RES SMD 3.3K OHM 1% 1/10W 0603 | 3.3k | RC0603FR-073K3L | Top
14 | R17, R18, R19, R22, R23, R24, R36, R37, R38, R40, R41, R42, R51, R54 | RES SMD 2.2 OHM 1% 1/10W 0603 | 2.2R | RC0603FR-072R2L | Top
1 | U1 | 3.3-V CAN Bus Transceiver |  | SN65HVD232D | Top
1 | U2 | ARM Cortex-M4 32-bit MCU+FPU, 210 DMIPS, 1024 kB Flash, 192 kB Internal RAM, 51 I/Os, 64-pin LQFP, -40 to 85 degC, Tray |  | STM32F405RGT6 | Top
1 | U3 | IC, LDO, REG, 3.3V, SOT223 | 3.3V | AP1117E33G-13 | Top
2 | U4, U5 | MOTOR DRIVER, 3PH, 56HTSSOP |  | DRV8301 | Top
1 | U6 | DRIVER, MOSFET, HALF BRIDGE, WSON-8, 1A |  | LM5109BSD/NOPB | Top

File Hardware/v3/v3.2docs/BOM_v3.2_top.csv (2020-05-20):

Quantity | Designator | Description | Comment | LibRef | Layer
1 | C29 | CAP TANT 68UF 16V 20% 2312 250mOhm | 68uF | T495C686M016ATE250 | Top
8 | C38, C39, C42, C53, C54, C57, C62, C64 | CAP CER 2200PF 50V NP0 0603 | 2200pF | GRM1885C1H222JA01D | Top
2 | C59, C63 | CAP CER 0.1UF 25V X7R 0603 | 0.10µF | GRM188R71E104KA01D | Top
2 | FID1, FID3 | 1mm Fiducial with 2mm soldermask, 3mm keepout | FIDUCIAL | FIDUCIAL | Top
12 | H1, H2, H3, H4, H5, H6, H7, H8, H9, H10, H11, H12 | M3 Hole with no copper |  | M3 Hole | Top
1 | J2 | Header, 5-Pin |  | Header 5 | Top
1 | J3 | Header, 18-Pin | Leftheader | Header 18 | Top
1 | J4 | Header, 12-Pin | Rightheader | Header 12 | Top
10 | J7, J8, J11, J12, J13, J16, J17, J18, J21, J22 | M3 Spade Terminal |  | M3 Spade Terminal | Top
2 | J9, J23 | MULTICOMP Wire-To-Board Terminal Block, 2, 600 V, 30 A, 24 AWG, 10 AWG |  | MC000054 | Top
2 | J14, J19 | TERMINAL BLOCK, WIRE TO BRD, 3POS, 10AWG |  | MC000051 | Top
28 | Q1, Q2, Q3, Q4, Q5, Q6, Q7, Q8, Q9, Q10, Q11, Q12, Q13, Q14, Q15, Q16, Q17, Q18, Q19, Q20, Q21, Q22, Q23, Q24, Q25, Q26, Q27, Q28 | MOSFET N-CH 30V 13A SO8FL |  | NTMFS4935NT1G | Top
2 | R2, R4 | RES SMD 22 OHM 1% 1/10W 0603 | 22R | RC0603FR-0722RL | Top
2 | R6, R52 | RES SMD 10K OHM 1% 1/10W 0603 | 10K | RC0603FR-0710KL | Top
3 | R12, R31, R49 | THERMISTOR 10K OHM NTC 0402 SMD | 10k | NCP15XH103F03RC | Top
1 | R13 | RES SMD 3.3K OHM 1% 1/10W 0603 | 3.3k | RC0603FR-073K3L | Top
14 | R17, R18, R19, R22, R23, R24, R36, R37, R38, R40, R41, R42, R51, R54 | RES SMD 2.2 OHM 1% 1/10W 0603 | 2.2R | RC0603FR-072R2L | Top
5 | R25, R30, R43, R48, R55 | RES SMD 120 OHM 1% 1/10W 0603 | 120R | RC0603FR-07120RL | Top
1 | U2 | ARM Cortex-M4 32-bit MCU+FPU, 210 DMIPS, 1024 kB Flash, 192 kB Internal RAM, 51 I/Os, 64-pin LQFP, -40 to 85 degC, Tray |  | STM32F405RGT6 | Top
1 | U3 | IC REG LDO 3.3V 1A SOT223 | 3.3V | AZ1117EH-3.3TRG1 | Top
2 | U4, U5 | MOTOR DRIVER, 3PH, 56HTSSOP |  | DRV8301 | Top
1 | U6 | DRIVER, MOSFET, HALF BRIDGE, WSON-8, 1A |  | LM5109BSD/NOPB | Top

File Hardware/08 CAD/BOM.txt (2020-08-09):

3DX_CUI_Supplier: CUI, Inc
3DX_CUI_Description: 5 Vdc, 1 A, 5 W, 8~36 Vdc Input Range
3DX_CUI_Model Number: V78E05-1000-SMT-TR

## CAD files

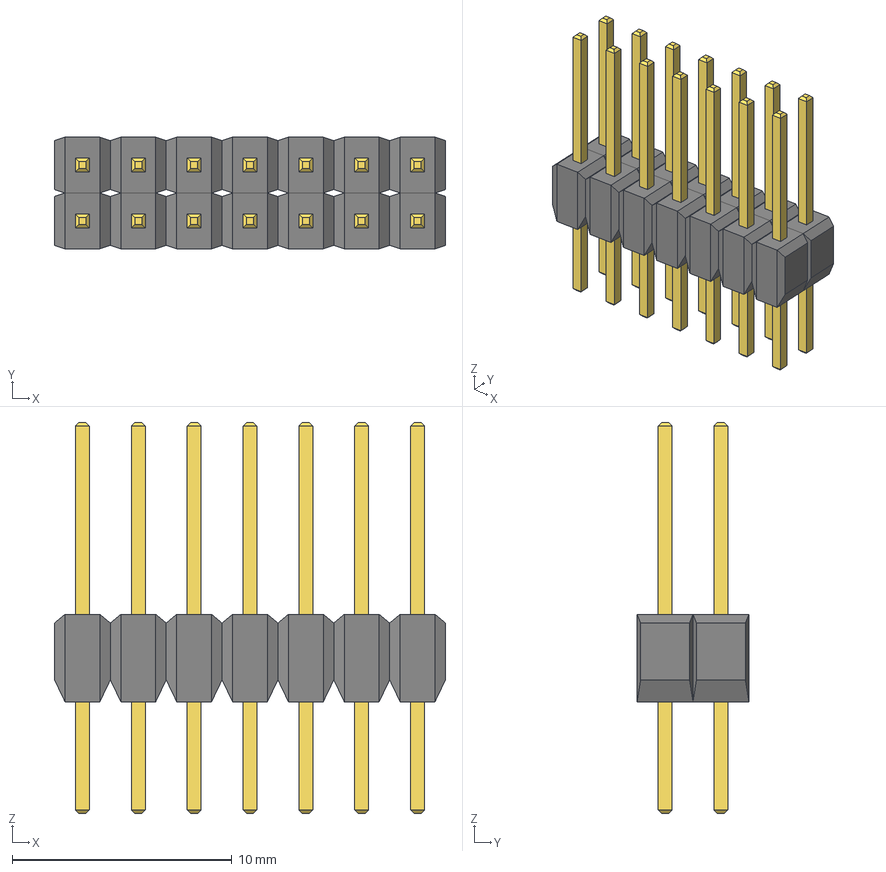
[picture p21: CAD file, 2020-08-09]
Hardware/08 CAD/2020-05-23_22-34-57/STEP/CON14_2X7_TU_TSW.step
17.8 x 5.08 x 17.8 mm

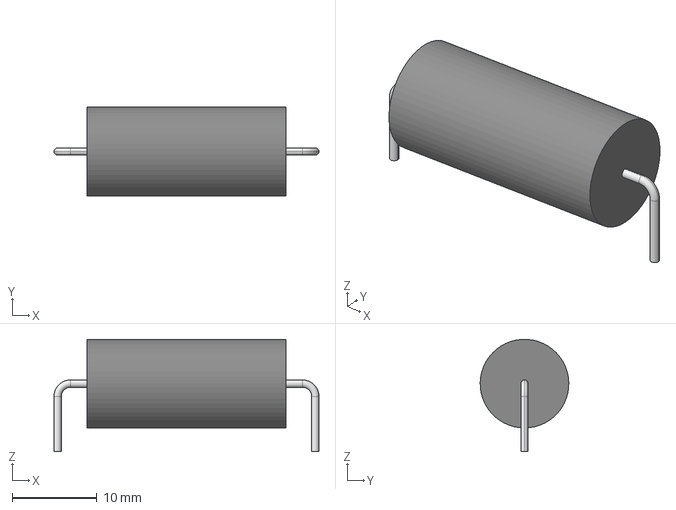
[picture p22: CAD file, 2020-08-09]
Hardware/08 CAD/2020-05-24_02-26-04/STEP/YAG_SQP500.step
31.3 x 10.5 x 13.3 mm

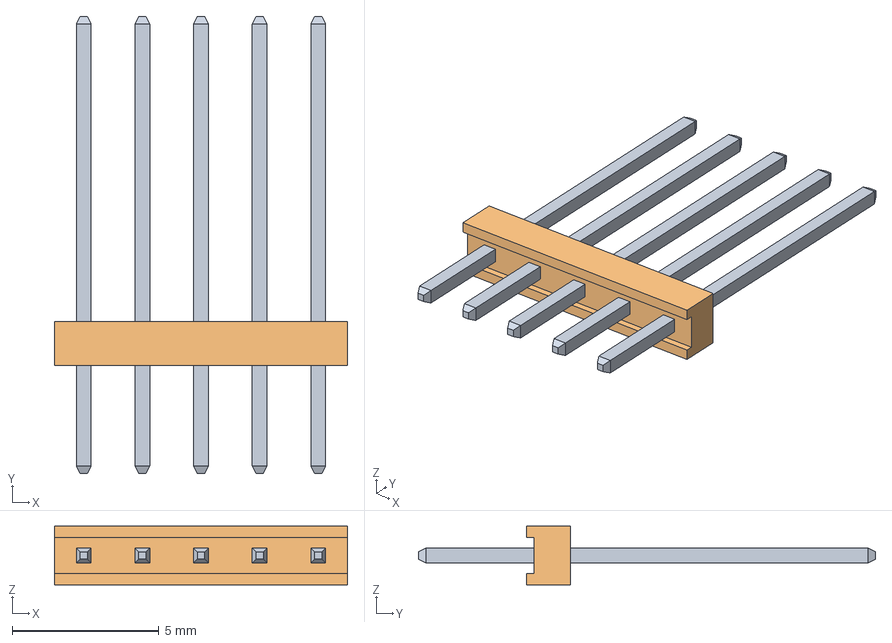
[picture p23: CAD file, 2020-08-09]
Hardware/08 CAD/MTMM-105-12-G-S-410.stp
10.00 x 15.6 x 2.00 mm
_MTMM-105-12-G-S-410_pins
_MTMM-105-12-G-S-410_body

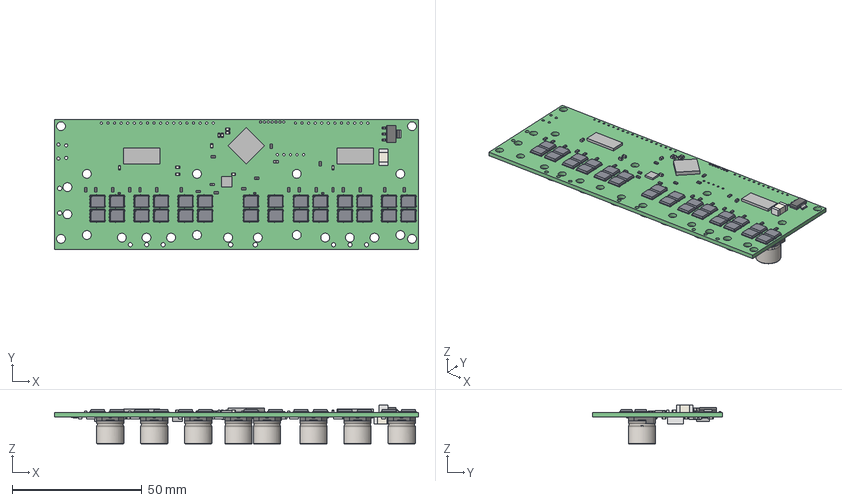
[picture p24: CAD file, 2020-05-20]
Hardware/v3/v3.2docs/PCB_v3.2.step
140.5 x 50.0 x 15.0 mm
Board
SOT23-5
Extruded x 201
RES_0402_(1005_metric) x 3
RES_0603_(1608_metric) x 48
SOT223-4
User_Library-DFN5x6_SO8FL_Extruded x 56
User_Library-DFN5x6_SO8FL_Extruded_2 x 56
User_Library-DFN5x6_SO8FL_Cylinder x 28
User_Library-DFN5x6_SO8FL_Extruded_3 x 28
User_Library-DFN5x6_SO8FL_Extruded_4 x 28
User_Library-DFN5x6_SO8FL_Extruded_5 x 112
User_Library-DFN5x6_SO8FL_Extruded_6 x 28
CAP_Alum_Elec_Size_G x 8

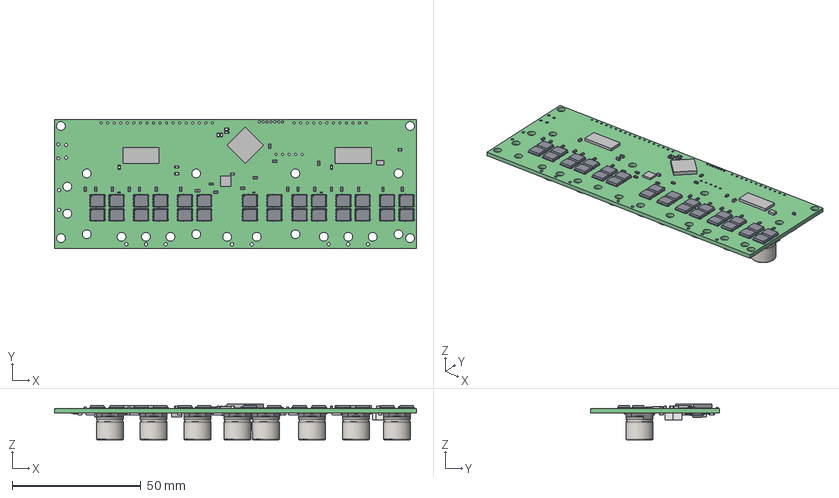
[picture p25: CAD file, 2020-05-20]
Hardware/v3/v3.3docs/PCB_v3.3.step
140.5 x 50.0 x 13.8 mm
Board
Extruded x 198
SOT23-5
RES_0402_(1005_metric) x 3
RES_0603_(1608_metric) x 47
SOT223-4
User_Library-DFN5x6_SO8FL_Extruded x 56
User_Library-DFN5x6_SO8FL_Extruded_2 x 56
User_Library-DFN5x6_SO8FL_Cylinder x 28
User_Library-DFN5x6_SO8FL_Extruded_3 x 28
User_Library-DFN5x6_SO8FL_Extruded_4 x 28
User_Library-DFN5x6_SO8FL_Extruded_5 x 112
User_Library-DFN5x6_SO8FL_Extruded_6 x 28
CAP_Alum_Elec_Size_G x 8
LED_0603_APT1608_GREEN

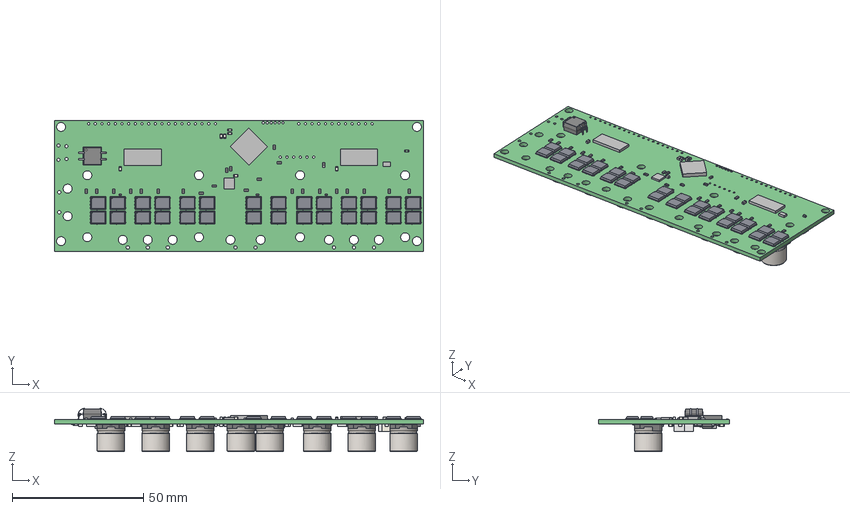
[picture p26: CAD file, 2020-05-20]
Hardware/v3/v3.5docs/PCB_v3.5.step
140.5 x 50.0 x 16.4 mm
Board
RES_0603_(1608_metric) x 53
Extruded x 206
Open_CASCADE_STEP_translator_6.8_2.1
Open_CASCADE_STEP_translator_6.8_2.2.1
Leader x 4
SOT23-5
RES_0402_(1005_metric) x 3
SOT223-4
User_Library-DFN5x6_SO8FL_Extruded x 56
User_Library-DFN5x6_SO8FL_Extruded_2 x 56
User_Library-DFN5x6_SO8FL_Cylinder x 28
User_Library-DFN5x6_SO8FL_Extruded_3 x 28
User_Library-DFN5x6_SO8FL_Extruded_4 x 28
User_Library-DFN5x6_SO8FL_Extruded_5 x 112
User_Library-DFN5x6_SO8FL_Extruded_6 x 28
CAP_Alum_Elec_Size_G x 8
LED_0603_APT1608_GREEN

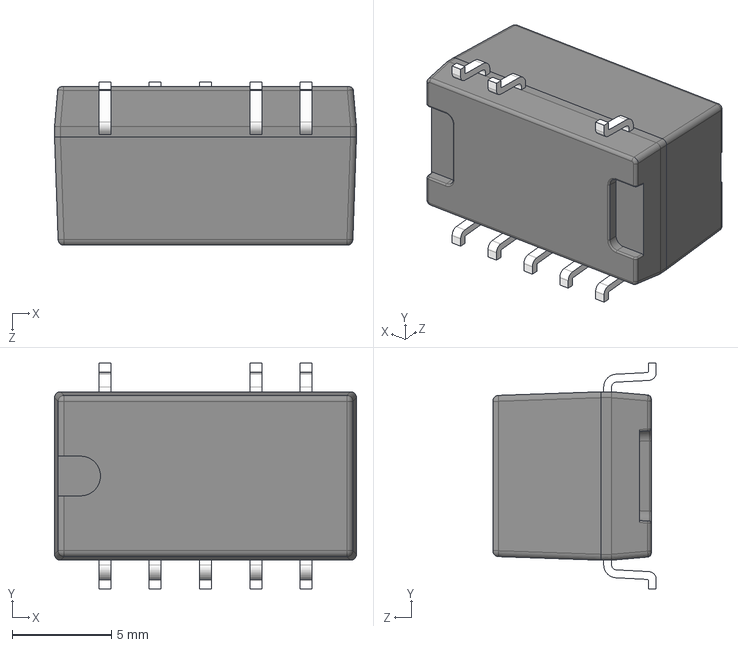
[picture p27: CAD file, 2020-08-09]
Hardware/08 CAD/CUI_V78E05-1000-SMT-TR.step
15.2 x 11.4 x 8.25 mm

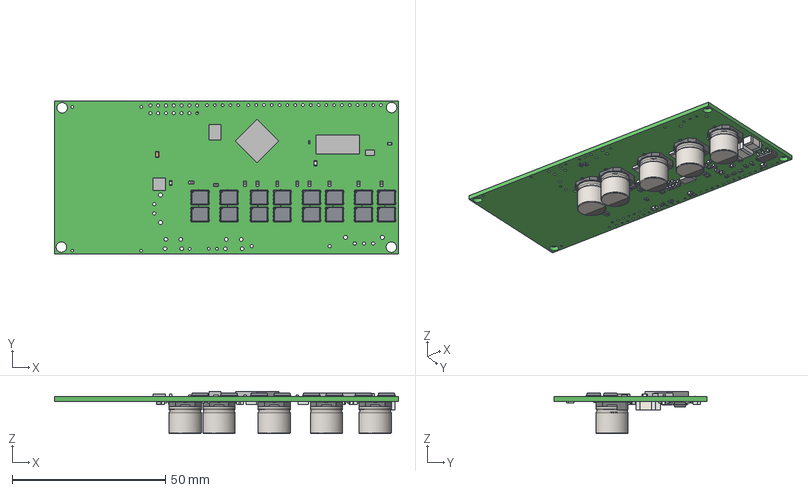
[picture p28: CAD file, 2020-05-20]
Hardware/08 CAD/BDDrive.step
112.1 x 50.0 x 13.8 mm
Extruded x 131
0805_SMD_Capacitor
1206_SMD_Resistor
SOT23-5
RES_0402_(1005_metric) x 2
RES_0603_(1608_metric) x 31
SOT223-4
User_Library-DFN5x6_SO8FL_Extruded x 32
User_Library-DFN5x6_SO8FL_Extruded_2 x 32
User_Library-DFN5x6_SO8FL_Cylinder x 16
User_Library-DFN5x6_SO8FL_Extruded_3 x 16
User_Library-DFN5x6_SO8FL_Extruded_4 x 16
User_Library-DFN5x6_SO8FL_Extruded_5 x 64
User_Library-DFN5x6_SO8FL_Extruded_6 x 16
CAP_Alum_Elec_Size_G x 5
LED_0603_APT1608_GREEN
J14
J9

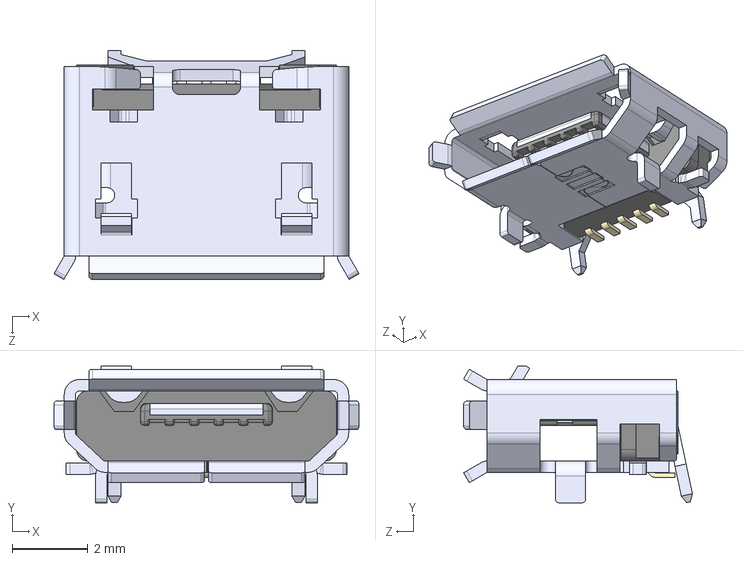
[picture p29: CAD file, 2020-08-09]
Hardware/08 CAD/10103594-0001LF--3DModel-STEP-56544.STEP
8.04 x 3.60 x 6.03 mm

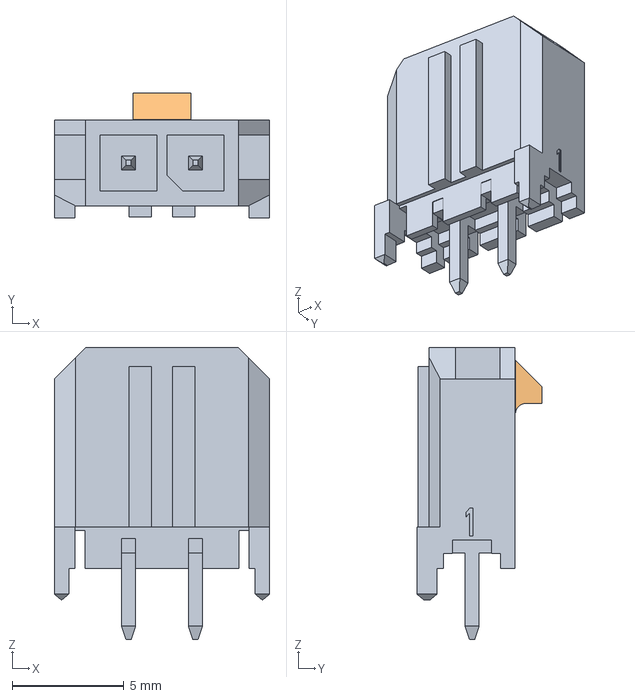
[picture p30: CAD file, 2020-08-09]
Hardware/08 CAD/436500227.stp
9.65 x 5.61 x 13.1 mm

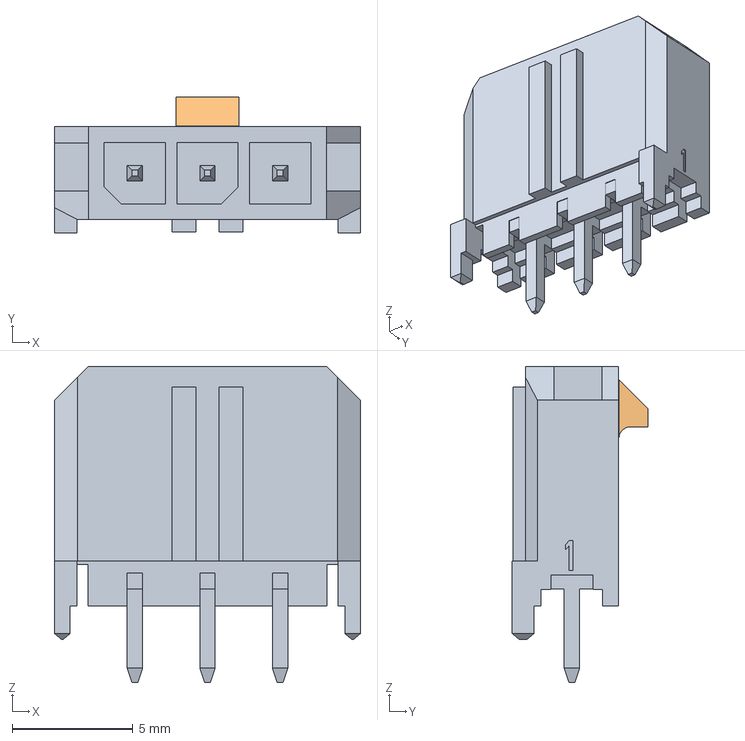
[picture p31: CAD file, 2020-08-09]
Hardware/08 CAD/436500327.stp
12.7 x 5.61 x 13.1 mm

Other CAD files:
Hardware/v3/v3.4docs/PCB_v3.4.step

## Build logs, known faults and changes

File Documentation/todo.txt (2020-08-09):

- via stiching
- production
- digikey
- check if based on v3.4 or v3.5 
- C1 not the same
- do general documentation document
- do README

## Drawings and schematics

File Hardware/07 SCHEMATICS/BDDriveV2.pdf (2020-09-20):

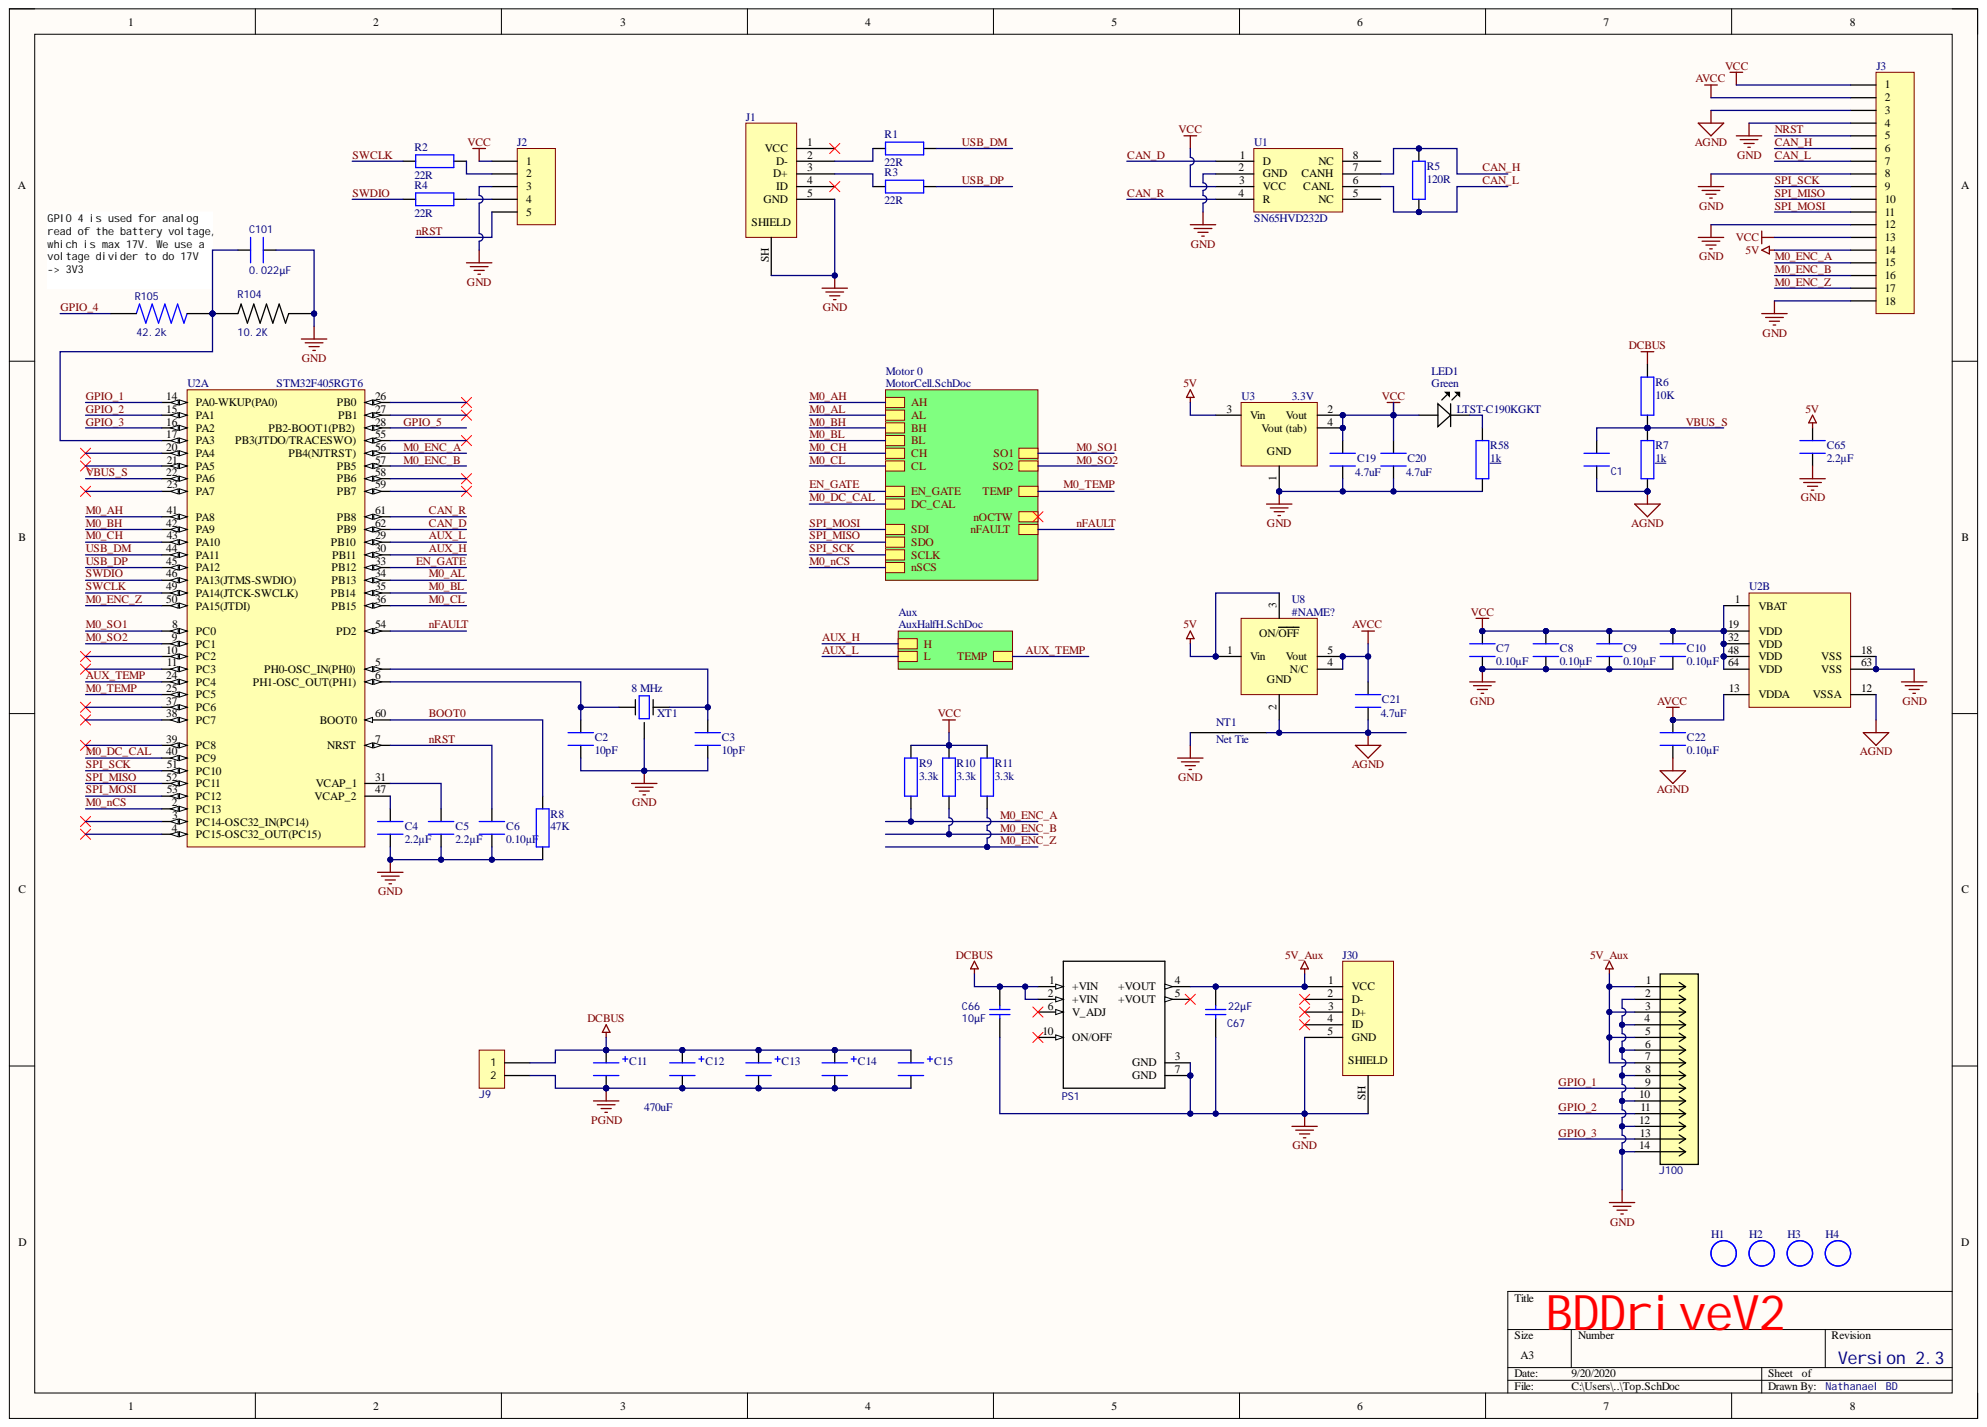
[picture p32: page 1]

GPIO 4 is used for analog
read of the battery voltage,
which is max 17V. We use a
voltage divider to do 17V

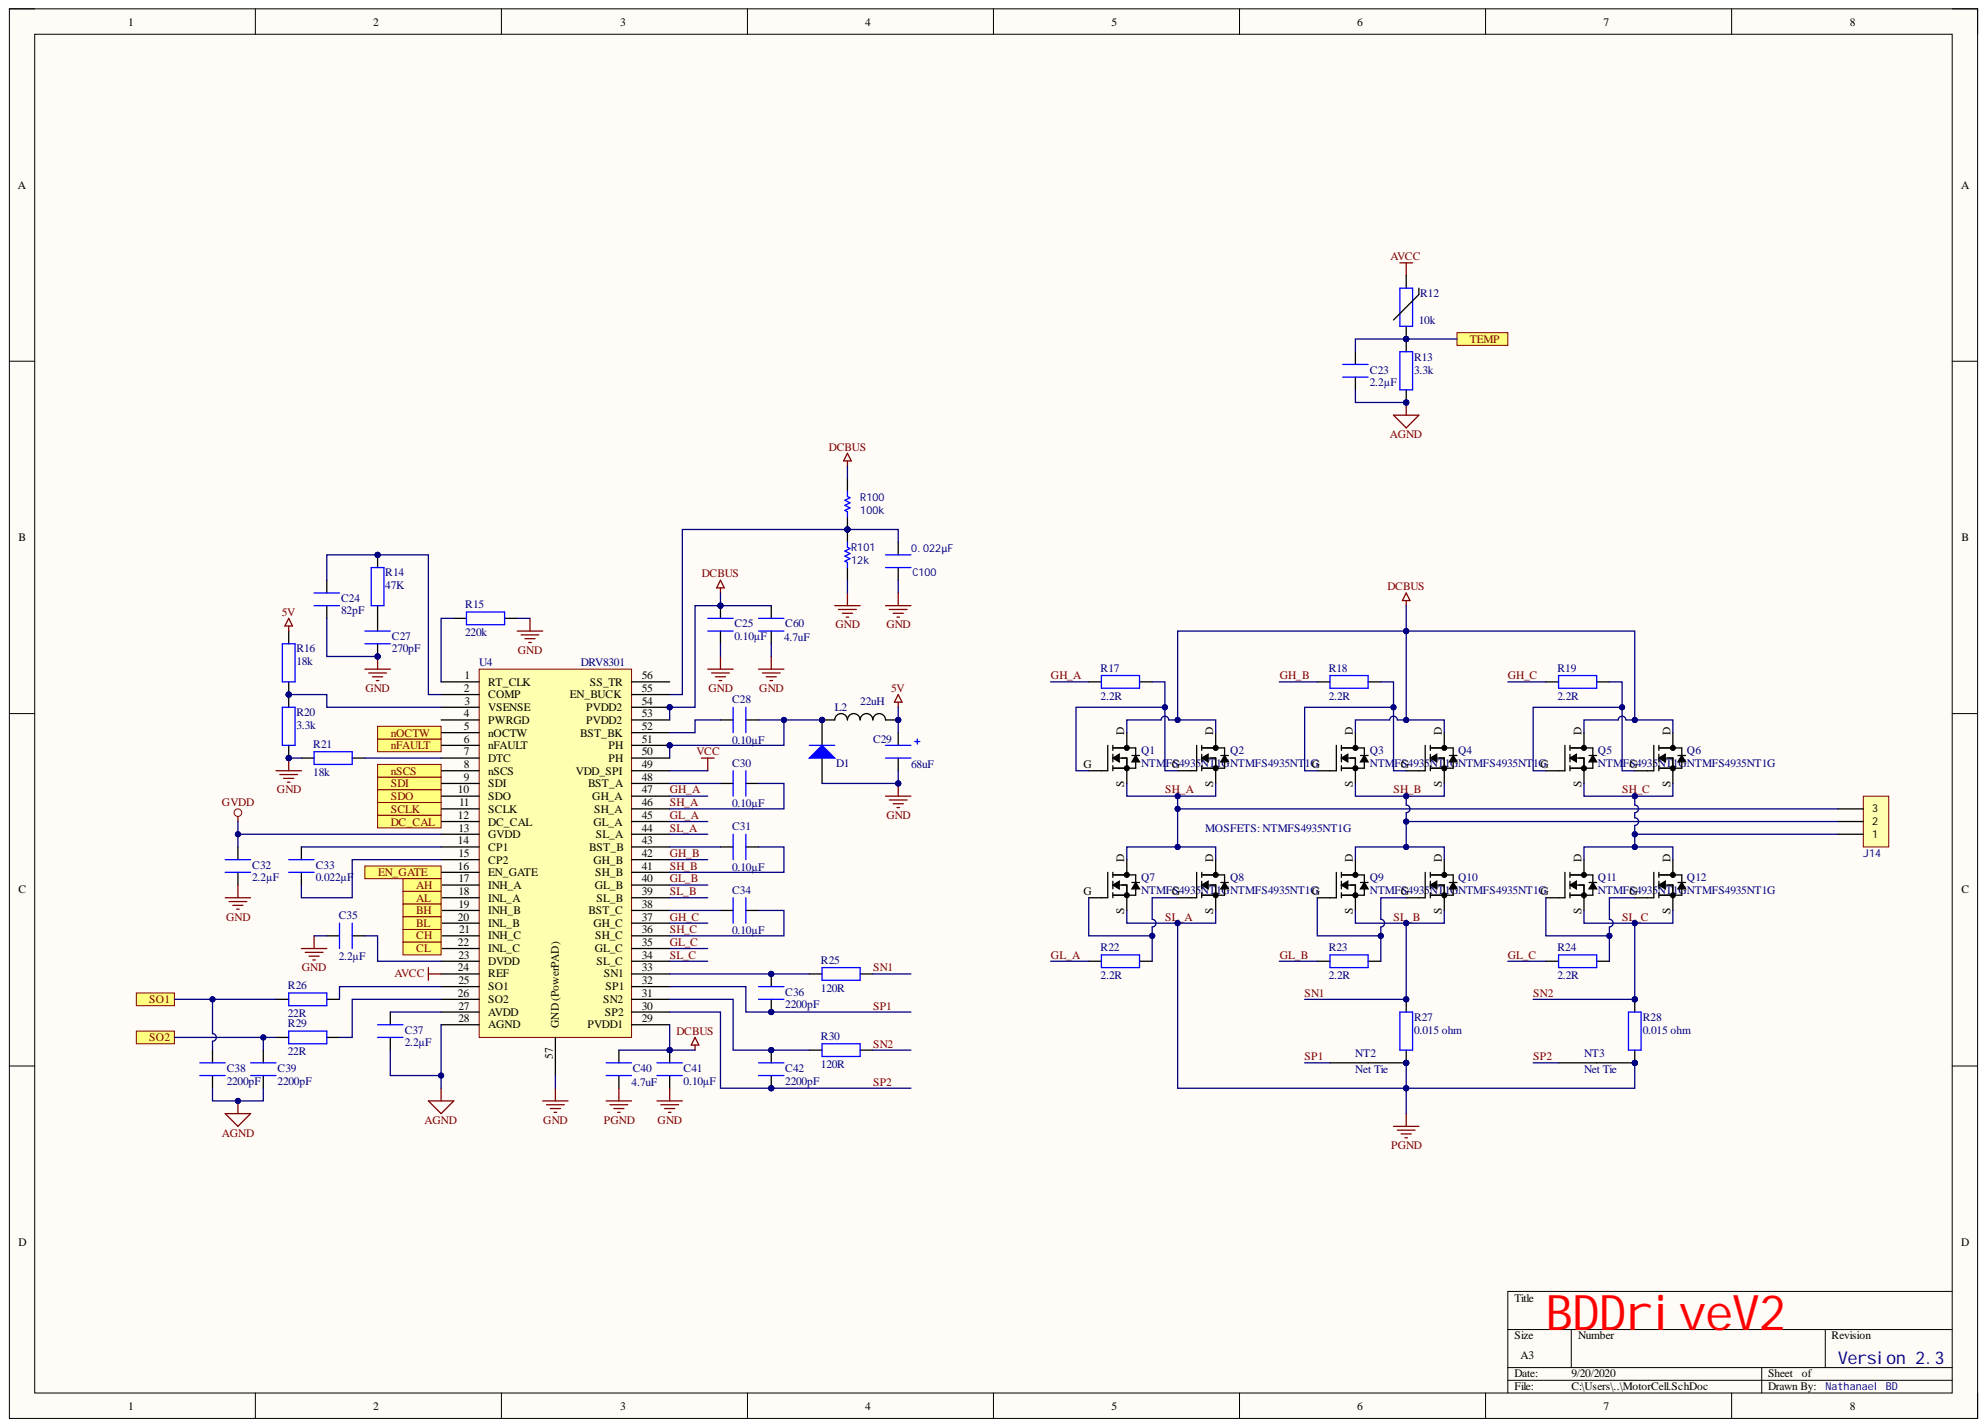
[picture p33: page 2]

n FAULT | 7 | | 5 0

1 4 | 4 3
1 5 | 4 2 | G H_ B | 0 . | 1 0 µ F
1 6 | 4 1 | S H_ B

EAHALBHBLCHCL | 1 9 | 3 8

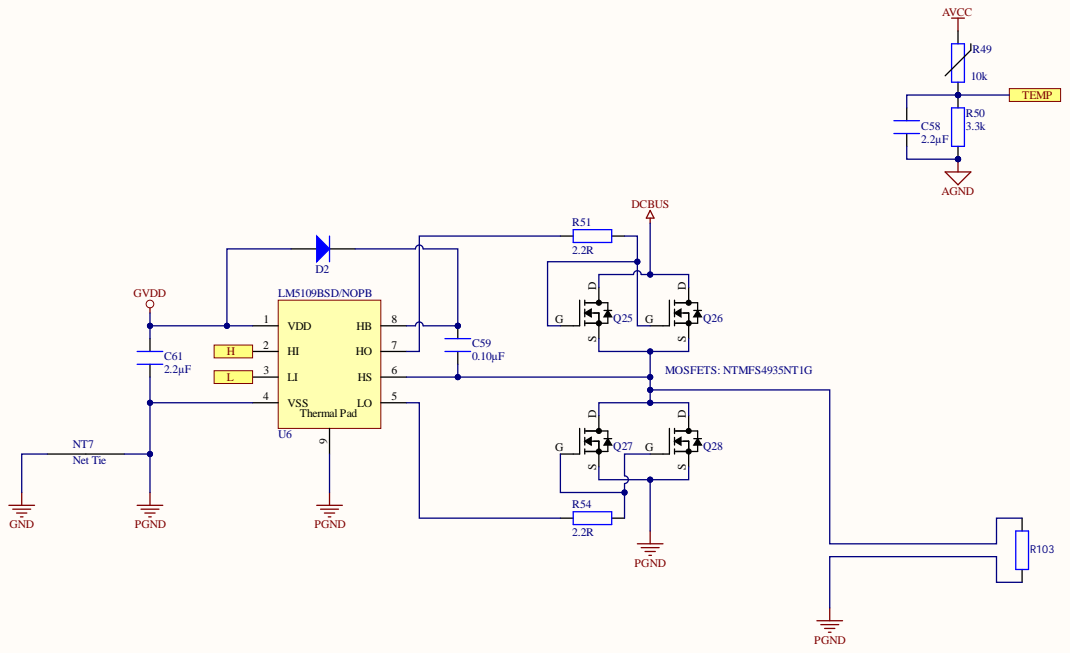
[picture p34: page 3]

VDD 1 HO HS Thermal Pad

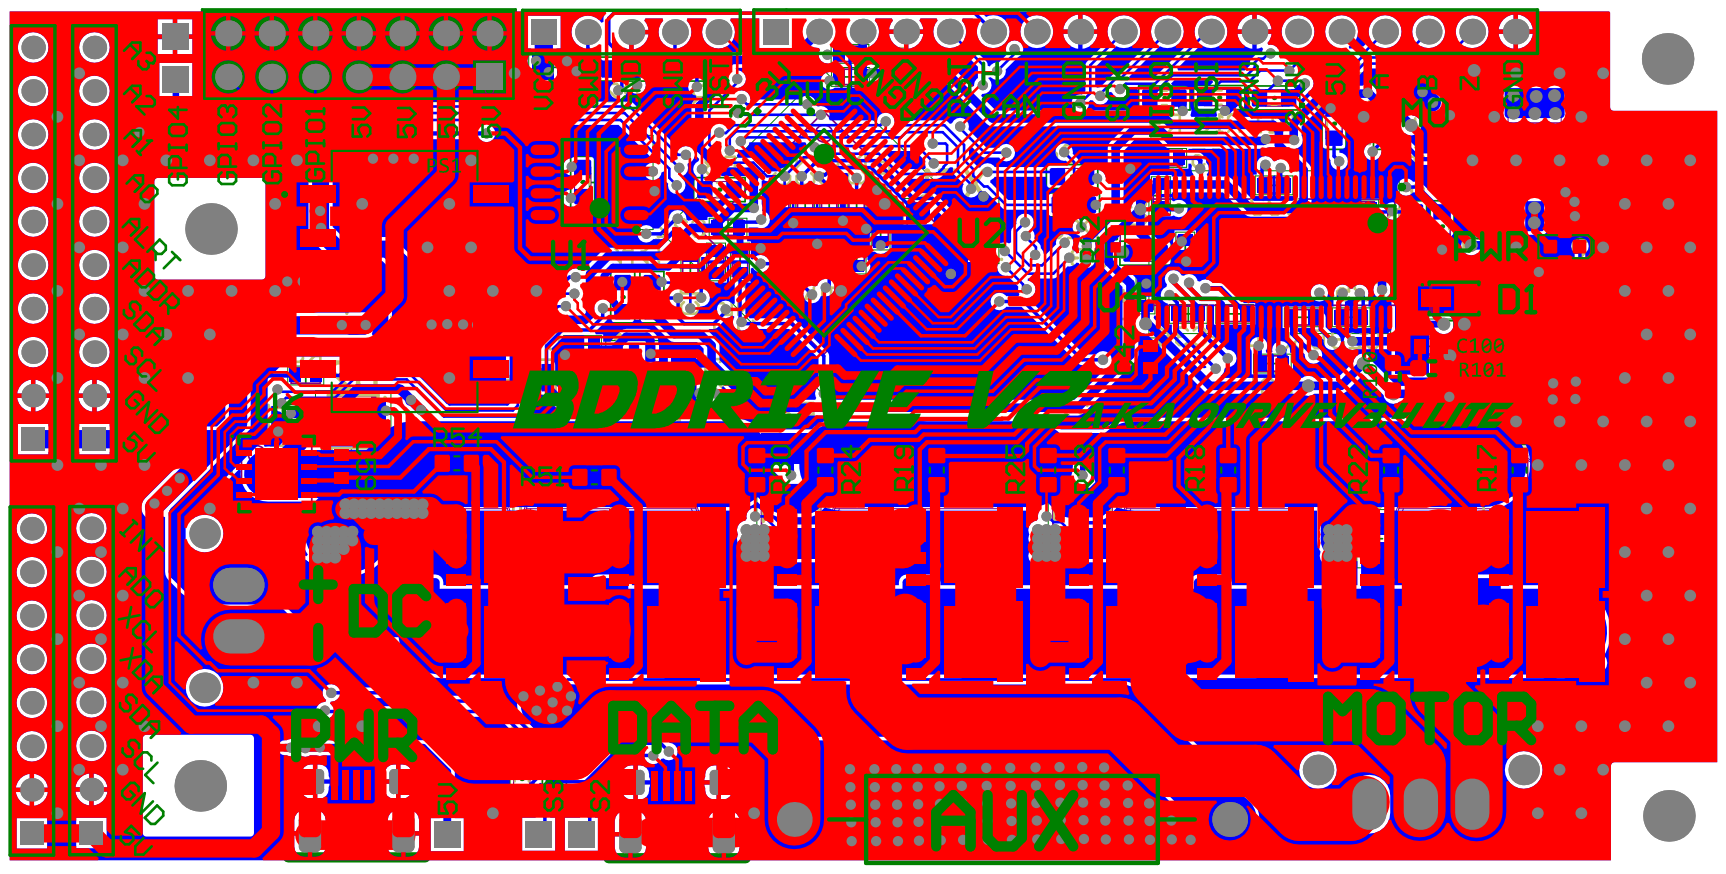
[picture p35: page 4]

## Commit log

2020-05-20 Add PCB and hardware folder
    [AuxHalfH.SchDoc, BDDrive.PrjPcb, BDDrive.step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]
2020-08-09 Add .step files
    [10103594-0001LF--3DModel-STEP-56544.STEP, 436500227.stp, 436500327.stp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]
2020-08-09 Add BOM
    [64345100.csv, BDDrive.csv]
2020-08-10 Update PCB
    [BDDrive.PrjPcb, CustomFootprints.PcbLib, Top.SchDoc]
2020-09-06 Add BDDrive pictures and schematic
2020-09-06 Update BDDrive with new specs
    [BDDrive.PrjPcb, two_ax_PCB.PrjPcb]
2020-09-06 Update BDDrive with new headers
    [CustomComponents.SchLib, CustomFootprints.PcbLib]
2020-09-06 Add 5V and GND routed to new headers
    [CustomFootprints.PcbLib]
2020-09-18 Finish v2
    [AuxHalfH.SchDoc, BDDrive.PrjPcb, CustomComponents.SchLib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]
2020-09-20 Production of BDDriveV2
    [AuxHalfH.SchDoc, BDDrive.PrjPcb, BDDriveV2.csv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]
2020-10-28 Update CAD version of BDDriveV2

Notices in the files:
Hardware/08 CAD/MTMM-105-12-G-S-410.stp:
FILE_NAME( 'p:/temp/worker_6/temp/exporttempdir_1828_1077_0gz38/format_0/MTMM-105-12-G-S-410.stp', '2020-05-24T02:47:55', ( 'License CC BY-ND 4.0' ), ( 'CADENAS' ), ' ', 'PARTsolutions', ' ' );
